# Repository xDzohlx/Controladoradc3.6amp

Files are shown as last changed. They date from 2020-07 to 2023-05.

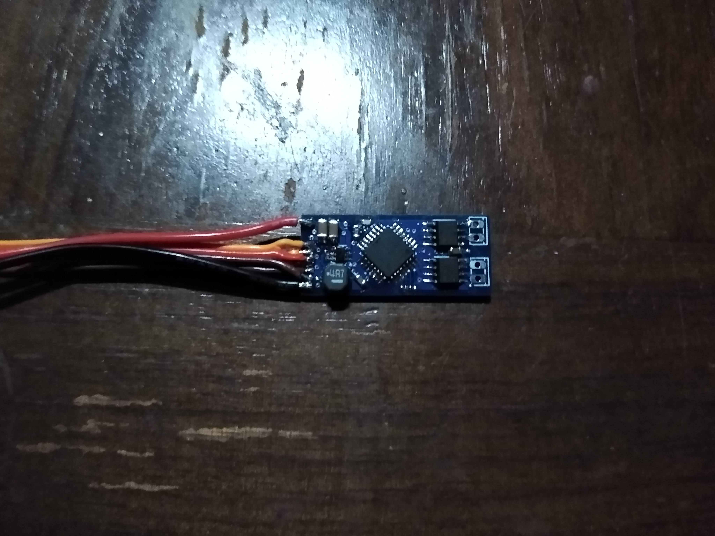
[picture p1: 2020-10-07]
imagenes/IMG_20200807_203210797.jpg

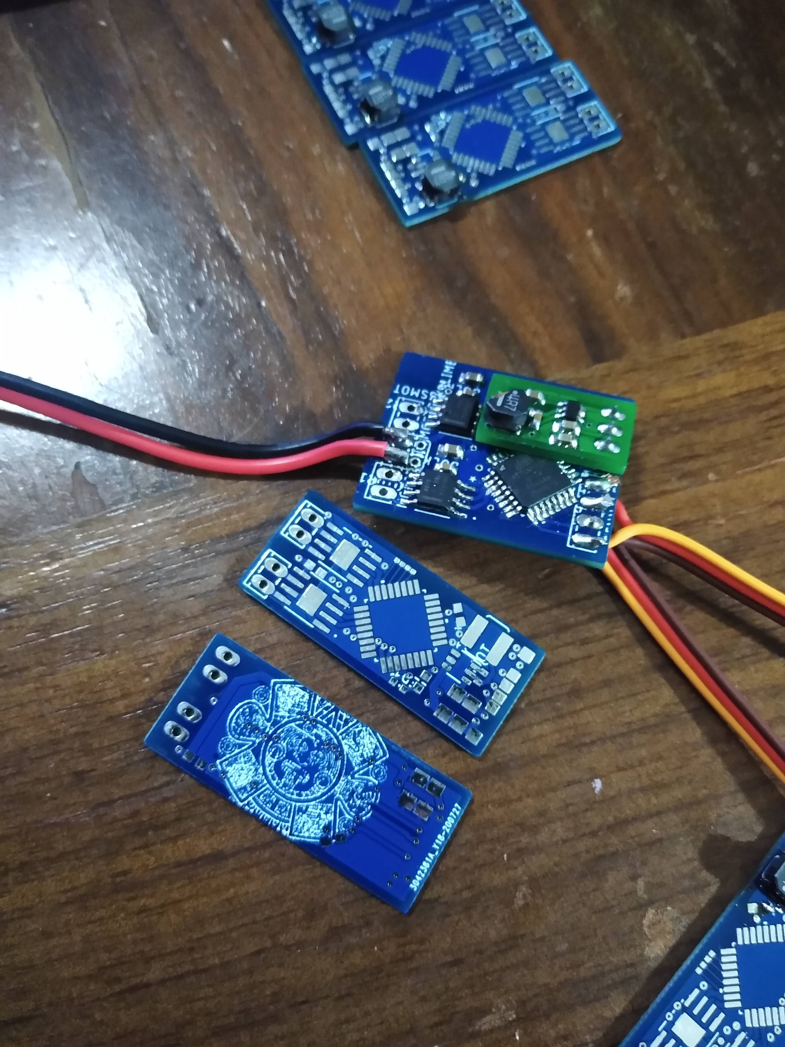
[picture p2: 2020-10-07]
imagenes/IMG_20200803_212737606.jpg

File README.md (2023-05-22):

# Controladoradc3.6amp
Controladora electronica de velocidad de 3.6 amperios hasta 25 volts V1.1
Controladora electronica de velocidad de 3.6 amperios hasta 25 volts V1.1 Esta es la versión 1.1 de la tarjeta controladora fue diseñada por Carlos Vega, la selección de componentes del driver y el microcontrolador por Aldo Bucio. Está basada en otra paca diseñada por Aldo bucio hace tiempo. Perdí el primer archivo de la placa pero estan los archivos gerber pero estan los de la version 1.1.

Especificaciones: 4 celdas de litio polímero, hasta 25 volts absolutos(por los capacitores de puede aumentar la tensión hasta 32 volts absolutos limitados por el regulador) 3.6 amperios por canal, protegida para más corriente se apaga y reinicia cuando se alcanza esta corriente. El driver de los motores es muy confiable y a prueba de balas lo que se necesita para el combate de robots Canales completamente mezclados para conducir un robot en modo diferencial. Se leen dos canales de pwm en cualquier protocolo de envío de 50 a 100 hz. También esta la version de firmware con lectura de ppm en un solo cable con decodificador de un canal para la activación de un servo u otro actuador. Los esquematicos y la placa estan diseñadas en Eagle.Fue programada en atmel studio 7 con el microcontrolador Attiny828.

Manual de operacion Caracteristicas

Gracias por usar la tarjeta controladora electrónica de velocidad. Características: Canal doble 3.6 A por canal Protección contra sobre corriente y sobre temperatura 2-6s de litio polímero 25 volts absolutos 7.2 Amp Canal doble Interfaz RC PWM, PPM Decodificador en modo PPM sin retraso. Canales mezclados o bidireccionales. Sin retraso de señal de radio Auto calibración al encendido BEC conmutada de alta eficiencia 88% 1 A hasta 2A continuos. (BEC) Respuesta lineal Adelante y atrás a máxima potencia. PWM de 32 Khz Freno del motor Tiempo de servicio muy largo puede estar encendida por más de 1 hr. Conector JST para batería. Conectores de servo para señales.

El modo de operación viene preprogramdo, como lectura independiente de PWM, PPM, mezclados, bidireccionales o canal sencillo de mayor corriente estos modos son el firmware de la controladora. Modo PWM. El canal 1 es el volate y el canal 2 es el acelerador, el primero controla los giros mientras que el segundo controla el acelerador y la reversa. Modo PPM. En el canal 1 se conecta la señal PPM, el canal 1 es el volante y el canal 2 es el acelerador. El cable del canal dos es un decodificador del canal 3. En cualquiera de los modos cuenta con auto calibración al encendido por lo que se tiene que dar un tiempo a esto de 5 segundos antes de mover cualquier valor del radiocontrol. El led muestra el estado de la controladora.
Un video probando la tarjeta: https://t.co/X4io4Tz9yK?amp=1

Otros videos arreglando issues:
https://youtube.com/live/U84N-yGLdbo?feature=share

https://youtube.com/live/5lfUKTcOBrQ?feature=share

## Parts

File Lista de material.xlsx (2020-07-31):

Qty | Value | Device | Package | Parts | Description | Link |  | 2.06
5 | 0.1 uf,22uf, | C-EUC0603 | C0603 | BOOT, BYPASS1, BYPASSMICRO, BYPASSMICRO2, BYPASSMOTOR2 | CAPACITOR, European symbol | https://www.digikey.com.mx/product-detail/es/kemet/C0603C104Z3VACTU/399-1100-1-ND/411375 | https://www.digikey.com.mx/product-detail/es/kemet/C0603C104Z3VACTU/399-1100-1-ND/411375 | 0.032
4 | 1~100uf | C-EUC1206 | C1206 | BULKALIMENTACION, BULKALIMENTACION1, BULKALIMENTACION2, BULKALIMENTACION3 | CAPACITOR, European symbol | https://www.digikey.com.mx/product-detail/es/C3216X5R1E476M160AC/445-8047-1-ND/2792164/?itemSeq=323217674 |  | 3.76
2 | 3,6 amp | DRV8870 | DDA0008H_N | DRIVERMOTOR1, DRIVERMOTOR2 | Driver de motores | https://www.digikey.com.mx/product-detail/es/texas-instruments/DRV8870DDAR/296-42660-1-ND/5455925 |  | 3.446
1 | Rojo | LEDCHIPLED_0603 | CHIPLED_0603 | LED1 | LED | https://www.digikey.com.mx/product-detail/es/osram-opto-semiconductors-inc/LS-Q976-NR-1/475-2512-1-ND/1802639 |  | 0.201
3 | 1kohm | R-EU_R0603 | R0603 | R1, R2, R3 | RESISTOR, European symbol | https://www.digikey.com.mx/product-detail/es/yageo/RC0603JR-071KL/311-1-0KGRCT-ND/729624 |  | 0.021
1 | AP63205WU-7SOIC_05WU-7_DIO-L | AP63205WU-7SOIC_05WU-7_DIO-L | SOIC_05WU-7_DIO-L | U1 | Regulador conmutado | https://www.digikey.com.mx/product-detail/es/diodes-incorporated/AP63205WU-7/AP63205WU-7DICT-ND/9858428 |  | 0.745
1 | ATTINY828 | ATTINY828 | QFN50P500X500X100-33N | U$1 | Microcontrolador | https://www.digikey.com.mx/product-detail/es/microchip-technology/ATTINY828-MUR/1611-ATTINY828-MURCT-ND/6833245 |  | 0.6052
1 | INDUCTOR4.7 | INDUCTOR4.7 | IND_NRS5030T100MMGJ_TAY | U$2 | Inductor 4.7 1 | https://www.digikey.com.mx/product-detail/es/taiyo-yuden/NRS5030T4R7MMGJV/587-3605-1-ND/4694114 |  | 0.509
Precio dollar | 22

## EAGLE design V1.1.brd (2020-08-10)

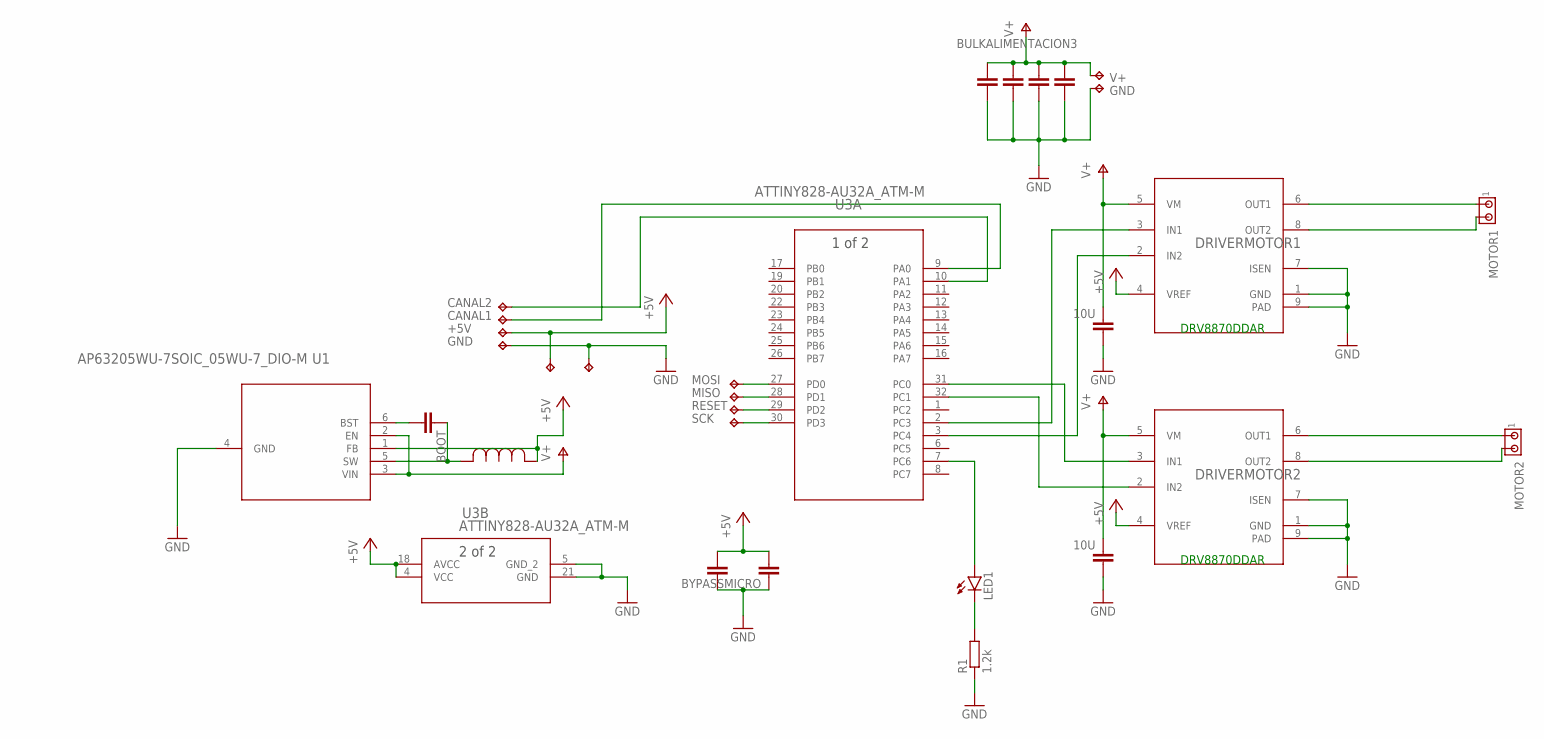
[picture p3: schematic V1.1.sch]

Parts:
BOOT: C-EUC0402; C0402
BULKALIMENTACION, BULKALIMENTACION1, BULKALIMENTACION2, BULKALIMENTACION3: C-EUC1206; C1206
BYPASS1: 10U; C0603
BYPASSMICRO, BYPASSMICRO2: C-EUC0603; C0603
BYPASSMOTOR2: 10U; C0603
DRIVERMOTOR1, DRIVERMOTOR2: DRV8870; DDA0008H_N
GND: TPTP20SQ; TP20SQ
LED1: LEDCHIPLED_0603; CHIPLED_0603
MISO: TPTP12R; TP12R
MOTOR1, MOTOR2: MTA02-100; 10X02MTA
R1: 1.2k; R0603
TP1, TP2, TP3, TP4, TP5, TP9: TPTP13SQ; TP13SQ
TP6, TP7, TP8: TPTP12R; TP12R
U1: AP63205WU-7SOIC_05WU-7_DIO-M; SOIC_05WU-7_DIO-M
U3: ATTINY828-AU32A_ATM-M; 32A_ATM-M
U$2: INDUCTOR4.7; IND_NRS5030T100MMGJ_TAY
V+: TPTP20SQ; TP20SQ

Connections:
+5V: BYPASSMICRO.2, BYPASSMICRO2.2, DRIVERMOTOR1.4 (VREF), DRIVERMOTOR2.4 (VREF), TP3.TP, TP9.TP, U1.1 (FB), U3.4 (VCC), U3.18 (AVCC), U$2.1
CANAL1: TP1.TP, U3.9 (PA0)
CANAL2: TP2.TP, U3.10 (PA1)
GND: BULKALIMENTACION.2, BULKALIMENTACION1.2, BULKALIMENTACION2.2, BULKALIMENTACION3.2, BYPASS1.1, BYPASSMICRO.1, BYPASSMICRO2.1, BYPASSMOTOR2.1, DRIVERMOTOR1.1 (GND), DRIVERMOTOR1.7 (ISEN), DRIVERMOTOR1.9 (PAD), DRIVERMOTOR2.1 (GND), DRIVERMOTOR2.7 (ISEN), DRIVERMOTOR2.9 (PAD), GND.TP, R1.1, TP4.TP, TP5.TP, U1.4 (GND), U3.5 (GND_2), U3.21 (GND)
MISO: TP6.TP, U3.28 (PD1)
MOSI: MISO.TP, U3.27 (PD0)
unnamed: DRIVERMOTOR1.3 (IN1), U3.2 (PC3)
unnamed: DRIVERMOTOR1.2 (IN2), U3.3 (PC4)
unnamed: DRIVERMOTOR2.3 (IN1), U3.31 (PC0)
unnamed: DRIVERMOTOR2.2 (IN2), U3.32 (PC1)
unnamed: DRIVERMOTOR2.8 (OUT2), MOTOR2.2
unnamed: DRIVERMOTOR2.6 (OUT1), MOTOR2.1
unnamed: DRIVERMOTOR1.8 (OUT2), MOTOR1.2
unnamed: DRIVERMOTOR1.6 (OUT1), MOTOR1.1
unnamed: LED1.A, U3.7 (PC6)
unnamed: LED1.C, R1.2
unnamed: BOOT.1, U1.5 (SW), U$2.2
unnamed: BOOT.2, U1.6 (BST)
RESET: TP7.TP, U3.29 (PD2)
SCK: TP8.TP, U3.30 (PD3)
V+: BULKALIMENTACION.1, BULKALIMENTACION1.1, BULKALIMENTACION2.1, BULKALIMENTACION3.1, BYPASS1.2, BYPASSMOTOR2.2, DRIVERMOTOR1.5 (VM), DRIVERMOTOR2.5 (VM), U1.2 (EN), U1.3 (VIN), V+.TP

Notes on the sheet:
DRV8870DDAR

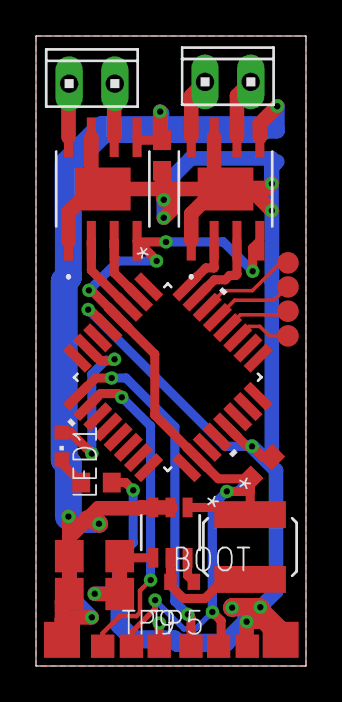
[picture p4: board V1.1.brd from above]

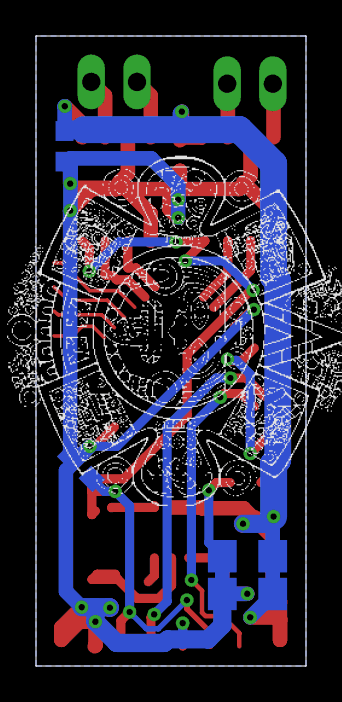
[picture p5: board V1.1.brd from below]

Board: 2 copper layers, 15.0 x 35.0 mm, 30 parts (4 on the bottom side), 21 nets.

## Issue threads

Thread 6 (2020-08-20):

Saturación de canales

xDzohlx, 2020-08-20:
Por el momento la saturación de canales no funciona bien al momento de estar en los valores mas bajos y mas altos se desborda el registro
OCR0 correspondiente. Se arregla fácilmente poniendo puntos máximos y mínimos en el radio control

xDzohlx, 2023-05-22:
Arreglado despues de 3 años despues de la ultima actualizacion

Closed 2023-05-22.

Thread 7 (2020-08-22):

sbus

xDzohlx, 2020-08-22:
Falta probar el código para sbus pero quiero probarlo con osciloscopio y no lo tengo disponible por el momento, solo tiene seguridad para checar errores por paridad y sincronización cada 6.5 ms para la espera de datos, no se acomodan los bytes y no esta implementado correctamente

xDzohlx, 2023-05-22:
No  se puede arreglar con el hardware actual, se rechaza el issue, se incluera en versiones de hardware superiores.

Closed 2023-05-22.

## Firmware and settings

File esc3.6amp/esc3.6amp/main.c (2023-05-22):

/*
 *main.cpp
 *
 * Created: 23/05/2017 23:52:50
 * Author : dzohl
 */ 

//detalles de version
//todavia no esta bien saturados los canales
//
//version acceptable y estable faltan limites inferiores se arregla desde el control con endpoints


//inputs canal 1 pa2, canal 2 pa3
//motores 


#include <avr/io.h>
#include <avr/interrupt.h>
#include <util/delay.h>
#include <stdbool.h>


volatile static uint16_t contador = 0x0000;
volatile static uint16_t contador2 = 0x0000;
volatile static uint16_t filtro_accel = 0x0000;
volatile static uint16_t accel = 0x0000;
volatile static uint16_t accel_val = 0x0000;
volatile static uint16_t accel_val_2 = 0x0000;
volatile static uint16_t accel_control = 0x0000;
volatile static uint16_t accel_control_2 = 0x0000;
volatile static uint16_t filtro_giro = 0x0000;
volatile static uint16_t giro = 0x0000;
volatile static uint16_t giro_val = 0x0000;
volatile static uint16_t giro_val_2 = 0x0000;
volatile static uint16_t giro_control = 0x00;
volatile static uint16_t giro_control_2 = 0x00;
volatile static uint16_t tiempo1 = 0x0000;
volatile static uint16_t tiempo2 = 0x0000;
volatile static uint16_t tiempo3 = 0x0000;
volatile static uint16_t canal_3 = 0x0000;
volatile static uint8_t motor1pwm = 0x00;
volatile static uint8_t motor2pwm = 0x00;
volatile static uint8_t ledpwm[2];
//volatile static uint16_t miliseg = 0x00;
uint16_t offsetgiro = 0x00;
uint16_t offsetaccel = 0x00;

bool primero = false;
bool segundo = false;
bool tercero = false;
bool button = true; 
bool canal = true; 
bool canal_1 = false;
bool canal_2 = false;
bool select_canal_1 = false;
bool select_canal_2 = false;
bool seleccion = false;
bool forward = false;
bool adelante = false;
bool forward_canal_2 = false;
bool right = false;
bool superbutton = false;
bool canal_1_valido = false;
bool canal_2_valido = false;
bool canal_3_valido = false;
bool failsafe = true;


void setup(){	
	//dos canales controlados por interrupcion
	DDRC = (1<<DDC4)|(1<<PORTC0)|(1<<PORTC3)|(1<<PORTC1)|(1<<PORTC6);
	PUEB = (1<<PORTB6)|(1<<PORTB4);
	PORTB = (1<<PORTB6)|(1<<PORTB4);
	PORTC |= (1<<PORTC6);
	//DDRA = (1<<PORTA0)|(1<<PORTA1);
	//PORTA |= (1<<PORTA1);//robot encendido
	//selecciondecanales();
	//interrupciones pines externos canal1
	PCICR = (1<<PCIE0);
	PCMSK0 |= (1<<PCINT0)|(1<<PCINT1);//|(1<<PCINT4);//interrucpciones canales
	//timer0 8 bit
	TCCR0A |= (1<<COM0A0)|(1<<COM0A1)|(1<<WGM00)|(1<<WGM01)|(1<<COM0B1)|(1<<COM0B0);
	TCCR0B |= (1<<CS00);

	TOCPMSA0 |= (1<<TOCC3S0);
	
	TOCPMSA1 |= (1<<TOCC4S0);
	
	TOCPMSA0 &= ~(1<<TOCC0S0);
	TOCPMSA0 &= ~(1<<TOCC1S0); 
	
	TOCPMCOE |= (1<<TOCC1OE);//motor a
	TOCPMCOE &= ~(1<<TOCC0OE);
	
	PORTC |=(1<<PORTC0);
	PORTC |=(1<<PORTC1);

	PORTC |=(1<<PORTC3);
	PORTC |=(1<<PORTC4);
		
	TOCPMCOE |= (1<<TOCC3OE);//motor b
	TOCPMCOE &= ~(1<<TOCC4OE);
	
	OCR0A = 0x00;
	OCR0B = 0x00;
	//TIMER1 16 BIT TIEMPOS contador de rc
	TCCR1A = 0x00;
	TCCR1B = (1<<WGM12)|(1<<CS11);//|(1<<CS10);
	
	OCR1A = 0xFF00;//validador de rc checar failsafe
	
	//TIMSK1 = (1<<TOIE1)|(1<<OCIE1A);
	
	TCNT1 = 0x0000;
	//selecciondecanales();
	sei();
	//parchada 
	_delay_ms(2000);
	_delay_ms(2000);
	_delay_ms(2000);
	_delay_ms(2000);
	_delay_ms(2000);
	giro_val = giro;
	filtro_giro = giro_val;
	_delay_ms(2000);
	accel_val = accel;
	filtro_accel = accel_val;
}
void pwmled(){
	if (TCNT0>=0&&primero){
		//PORTC |= (1<<PORTC6);
		primero = false;
		ledpwm[0]++;
		if (segundo){
			PORTC |= (1<<PORTC6);
			}else{
			PORTC &= ~(1<<PORTC6);
		}
	}
	if (TCNT0>=ledpwm[0]&&!primero){
		//PORTC &= ~(1<<PORTC6);
		primero = true;
		if (segundo){
			PORTC &= ~(1<<PORTC6);
			}else{
			PORTC |= (1<<PORTC6);
		}
	}
	if (ledpwm[0]==255&&tercero){
		segundo = !segundo;
		tercero=false;
	}
	if (ledpwm[0]==0){
		tercero = true;
	}
}
//INTERRUPCIONES PARA LECTURA DE RC
//inputs canal 1 pa2, canal 2 pa3
ISR(PCINT0_vect){
//funciona de forma sincrona ESTA PARCHADO
if (!(PINA & 0x02)){
	if (canal_1_valido){
		if(tiempo1< TCNT1)//ESTO ES UN PARCHE
		giro = TCNT1 - tiempo1;//lectura 1
		canal_1_valido = false;
		failsafe  = false;
	}
} else{
	if (canal){
		TCNT1 = 0x0000;
		canal = false;
	}
	if (!canal_1_valido){
		tiempo1 = TCNT1;//lectura 2
		canal_1_valido = true;
	}
}
//lectura 2
if (!(PINA & 0x01)){
	if (canal_2_valido){
		if(tiempo2< TCNT1)//ESTO ES UN PARCHE
		accel = TCNT1 - tiempo2;//lectura 1
		canal_2_valido = false;
	}
	} else{
	if (canal){
		TCNT1 = 0x0000;
		canal = false;
	}
	if (!canal_2_valido){
		tiempo2 = TCNT1;//lectura 2
		canal_2_valido = true;
	}
	//reset contador
	if (!(PINA & 0x02)&&!(PINA & 0x01)){
		canal = true;
		TCNT1 = 0x0000;
	}
}
//arm
//if (!(PINA & 0x10)){
	//if (canal_3_valido){
		//canal_3 = TCNT1 - tiempo3;
		//canal_3_valido = false;
	//}
	//} else{
	//if (!canal_3_valido){
		//tiempo3 = TCNT1;//lectura 2
		//canal_3_valido = true;
	//}
//}
}
//contador useg
ISR(TIMER1_COMPA_vect){
	failsafe  = true;
}
int main(void){
	setup();
	//PORTA &= ~(1<<PORTA1);
	while(1){
		//falta failsafe
	while(1){
		
			giro_control = giro;
			accel_control = accel;
			
		if (giro_control >= giro_val){// sentido del volante
			giro_control = giro_control-giro_val;//offset
			accel_control_2 = accel_control - giro_control;//motor 1
			accel_control = accel_control + giro_control;//motor 1
			}else{
			giro_control = giro_val - giro_control;//offset
			accel_control_2 = accel_control + giro_control;//motor 2
			accel_control = accel_control - giro_control;//motor 2
		}


//------------------------Motores
		if (accel_control>=accel_val){//MOTOR A

			accel_val_2 = accel_control - accel_val;
			if (accel_val_2>510)
			{
				accel_val_2 = 510;
			}
			accel_val_2 = accel_val_2>>1;//
			TOCPMCOE |= (1<<TOCC0OE);//motor a
			TOCPMCOE &= ~(1<<TOCC1OE);
			TCCR0A |= (1<<COM0A0);

			OCR0A = accel_val_2;
			}else{
				accel_val_2=accel_val-accel_control;
				if (accel_val_2>510)
				{
					accel_val_2 = 510;
				}
			accel_val_2 = accel_val_2>>1;

			TOCPMCOE |= (1<<TOCC1OE);//motor a
			TOCPMCOE &= ~(1<<TOCC0OE);
			//TCCR0A &= ~(1<<COM0A0);			
			OCR0A = accel_val_2;
		}
		
		if (accel_control_2>=accel_val){//MOTOR B
			//PORTA &= ~(1<<PORTA1);//arm
			
			giro_val_2 = accel_control_2 - accel_val;
			if (giro_val_2>510)
			{
				giro_val_2 = 510;
			}
			giro_val_2 = giro_val_2>>1;
			TOCPMCOE |= (1<<TOCC3OE);//motor
			TOCPMCOE &= ~(1<<TOCC4OE);

			OCR0B = giro_val_2;
			}else{
			giro_val_2=accel_val-accel_control_2;
			if (giro_val_2>510)
			{
				giro = 510;
			}
			giro_val_2 = giro_val_2>>1;

			TOCPMCOE |= (1<<TOCC4OE);//motor
			TOCPMCOE &= ~(1<<TOCC3OE);
			//TCCR0A &= ~(1<<COM0A0);
			OCR0B = giro_val_2;
		}	
		pwmled();
		}//arm
	OCR0A = 0x00;//hard stop
	OCR0B = 0x00;
	TOCPMCOE &= ~(1<<TOCC0OE);//motor a
	TOCPMCOE &= ~(1<<TOCC1OE);
	TOCPMCOE &= ~(1<<TOCC3OE);//motor a
	TOCPMCOE &= ~(1<<TOCC4OE);
	PORTC |= (1<<PORTC0)|(1<<PORTC1)|(1<<PORTC3)|(1<<PORTC4);
	//PORTA &= ~(1<<PORTA0);
	}//WHILE
}//INT MAIN

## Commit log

2020-08-04 Lecutura y mezclado de dos canales
    Este es el codigo original donde se leen dos canales de pwm de rc y se mezclan, se mandan señales de pwm para el control de dos motores
2020-08-04 PPM
    Este codigo puede leer hasta 6 canales de PPM de rc, mezcla dos canales y manda por pwm señal para control de dos motores
2020-08-04 PWM
    Lee y mezcla dos canales de pwm para mandar señal de pwm para control de motores
2020-08-10 Add files via upload
    se agrego pwm al led que muestra que no solo esta encendía sino que esta funcionando
2020-08-10 V1.2
    El esquemático es el mismo, la placa tiene mejores tolerancias, mejor distribución nuevos pads para señales y cumple con las especificaciones de jlcpcb
    [V1.1.brd, V1.1.sch]
2021-01-03 Update main.cpp
    Agregue el decodificador de ppm para una salida
2021-04-03 Version mezcla
    Programacion de esc mezclada en c++

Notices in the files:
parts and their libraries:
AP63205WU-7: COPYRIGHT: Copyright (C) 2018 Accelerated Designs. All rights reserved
